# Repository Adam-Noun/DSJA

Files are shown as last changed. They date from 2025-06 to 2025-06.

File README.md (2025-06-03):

Dual Synthetic Jet Actuator 

The proposed capstone project aims to design, fabricate, and experimentally test the performance of a dual 
synthetic jet actuators (SJAs) for flow control in a water tank. SJAs are innovative devices used for fluidic 
active flow control, with applications in aerospace and ground vehicles, electronic device cooling, jet 
vectoring, and mixing in fluid thermal systems. The project will focus on hands-on machining and 
manufacturing to create cost-effective dual SJAs with adjustable exit spacing.

Initial 3D printed Prototype of the device with different orifice geometry to test the effect that it would yield


Testing the deflection of the Piezoelectric Diaphragm with a 3D printed Jig with different weights ontop:



The assembly process of the Final design version of the DSJA: 



Testing Phase of the DSJA where ink would be injected and vortices would be recorded:



Different configuration (vertical or hortizontal) to record if there is any variance that the DSJA would experience depending on the orientation of the device.
[Assembly Experiment.pdf](https://github.com/user-attachments/files/20562680/Assembly.Experiment.pdf)

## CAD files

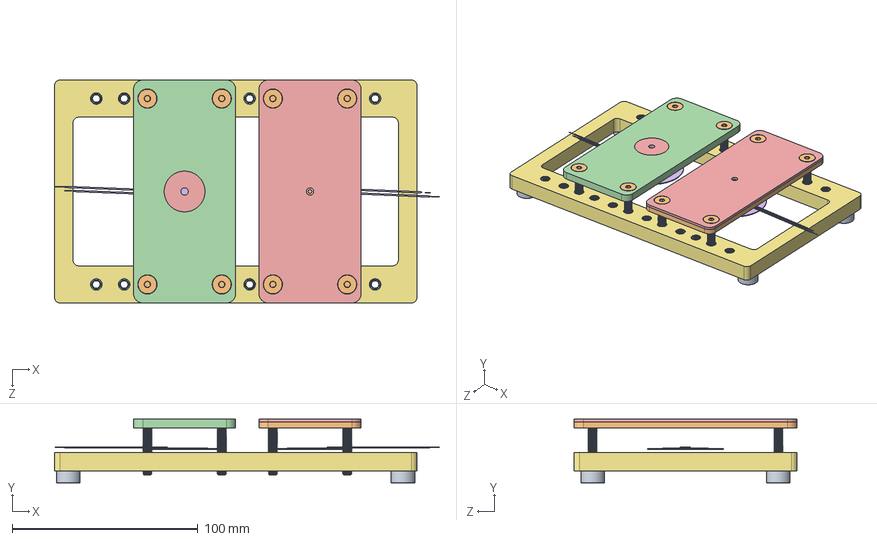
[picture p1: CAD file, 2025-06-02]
PRIMARY ASSEMBLY.SLDASM
207.1 x 34.4 x 120.0 mm
ORIFICE 2 (CIRCULAR) (DEPENDENT) x 2
7BB-41-2L0.stp x 2
FRAME ONE UNIT
Insert M5 D7 L9.5mm x 24
9540K11_Unthreaded Bumper x 4
91263A882_Zinc-Plated Alloy Steel Hex Drive Flat Head Screw x 8

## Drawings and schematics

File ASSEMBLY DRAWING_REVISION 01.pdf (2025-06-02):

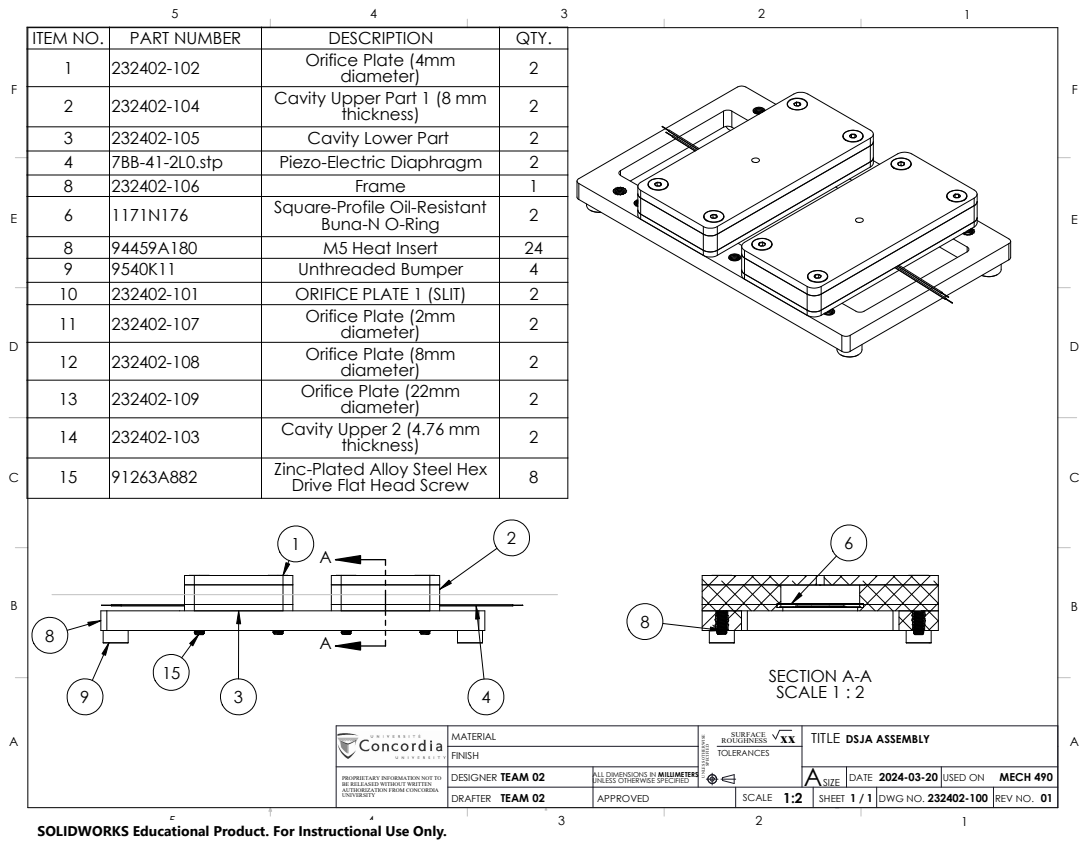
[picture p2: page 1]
TEAM 02; DWG NO.; USED ON; MECH 490; ASIZE; DRAFTER; APPROVED; SCALE 1:2; SHEET; REV NO. 1 / 1; DATE 2024-03-20; DESIGNER; SECTION A-A SCALE 1 : 2

ITEM NO. | PART NUMBER | DESCRIPTION | QTY.
1 | 232402-102 | Orifice Plate (4mm diameter) | 2
2 | 232402-104 | Cavity Upper Part 1 (8 mm thickness) | 2

3 | 232402-105 | Cavity Lower Part | 2
4 | 7BB-41-2L0.stp | Piezo-Electric Diaphragm | 2
8 | 232402-106 | Frame | 1
6 | 1171N176 | Square-Profile Oil-Resistant Buna-N O-Ring | 2

8 | 94459A180 | M5 Heat Insert | 24
9 | 9540K11 | Unthreaded Bumper | 4
10 | 232402-101 | ORIFICE PLATE 1 (SLIT) | 2
11 | 232402-107 | Orifice Plate (2mm diameter) | 2
12 | 232402-108 | Orifice Plate (8mm diameter) | 2
13 14 | 232402-109 232402-103 | Orifice Plate (22mm diameter) Cavity Upper 2 (4.76 mm thickness) | 2 2

15 | 91263A882 | Zinc-Plated Alloy Steel Hex Drive Flat Head Screw | 8

BE RELEASED WITHOUT WRITTEN PROPRIETARY INFORMATION NOT TO | MATERIAL | UNLESS OTHERWISE SPECIFIED | TITLE DSJA ASSEMBLY

UNLESS OTHERWISE SPECIFIED ALL DIMENSIONS IN TEAM 02 MILLIMETERS FINISH | ROUGHNESS SURFACE xx TOLERANCES

AUTHORIZATION FROM CONCORDIA
UNIVERSITY

SOLIDWORKS Educational Product. For Instructional Use Only.

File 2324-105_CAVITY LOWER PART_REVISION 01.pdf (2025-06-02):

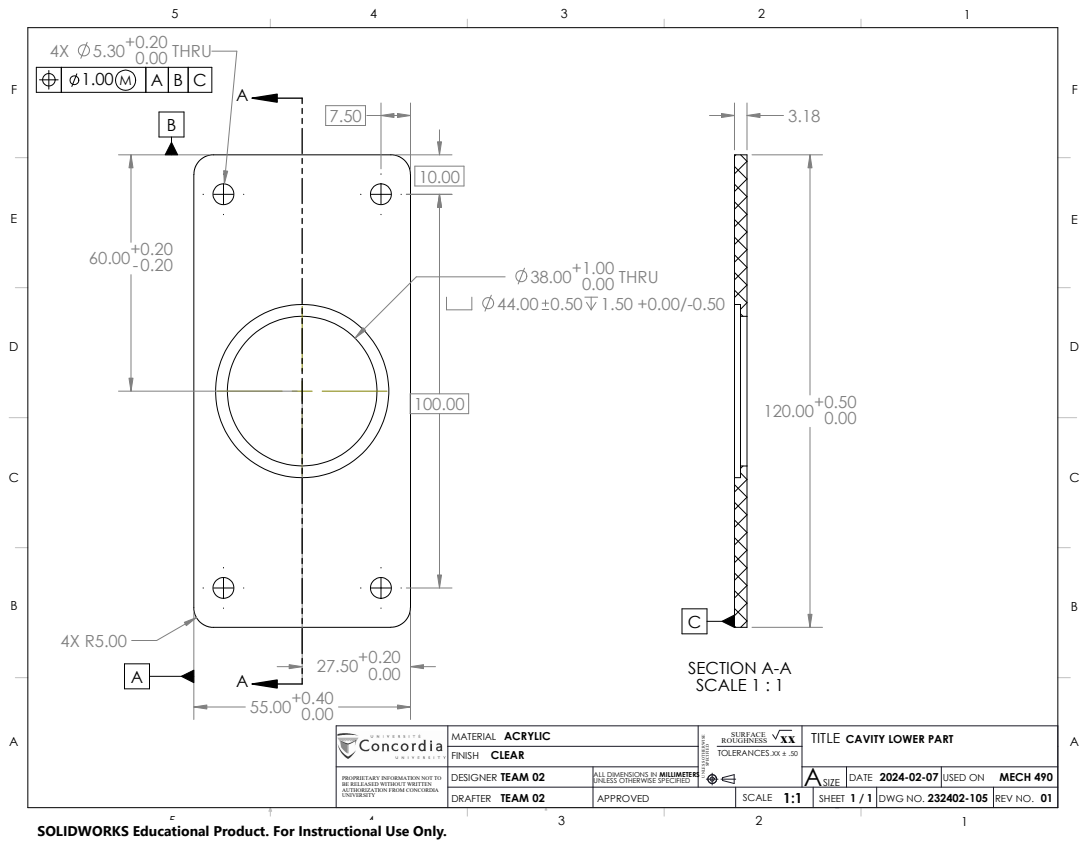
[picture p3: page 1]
TEAM 02; MILLIMETERS SPECIFIED; ACRYLIC; BE RELEASED WITHOUT WRITTEN; UNLESS OTHERWISE SPECIFIED; UNLESS OTHERWISE; ROUGHNESS; DWG NO.; USED ON; MECH 490; FINISH; ASIZE; TOLERANCES.XX ± .50; DRAFTER; APPROVED; SCALE 1:1; SHEET; REV NO. 1 / 1; DATE 2024-02-07; MATERIAL; DESIGNER; PROPRIETARY INFORMATION NOT TO; ALL DIMENSIONS IN; SURFACE; CLEAR; SECTION A-A SCALE 1 : 1; THRU 0.00 4X; 38.00+1.00 0.00 THRU 44.00 0.50

TITLE
CAVITY LOWER PART

AUTHORIZATION FROM CONCORDIA
UNIVERSITY

SOLIDWORKS Educational Product. For Instructional Use Only.

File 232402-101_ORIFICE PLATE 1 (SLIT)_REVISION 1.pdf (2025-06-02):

A

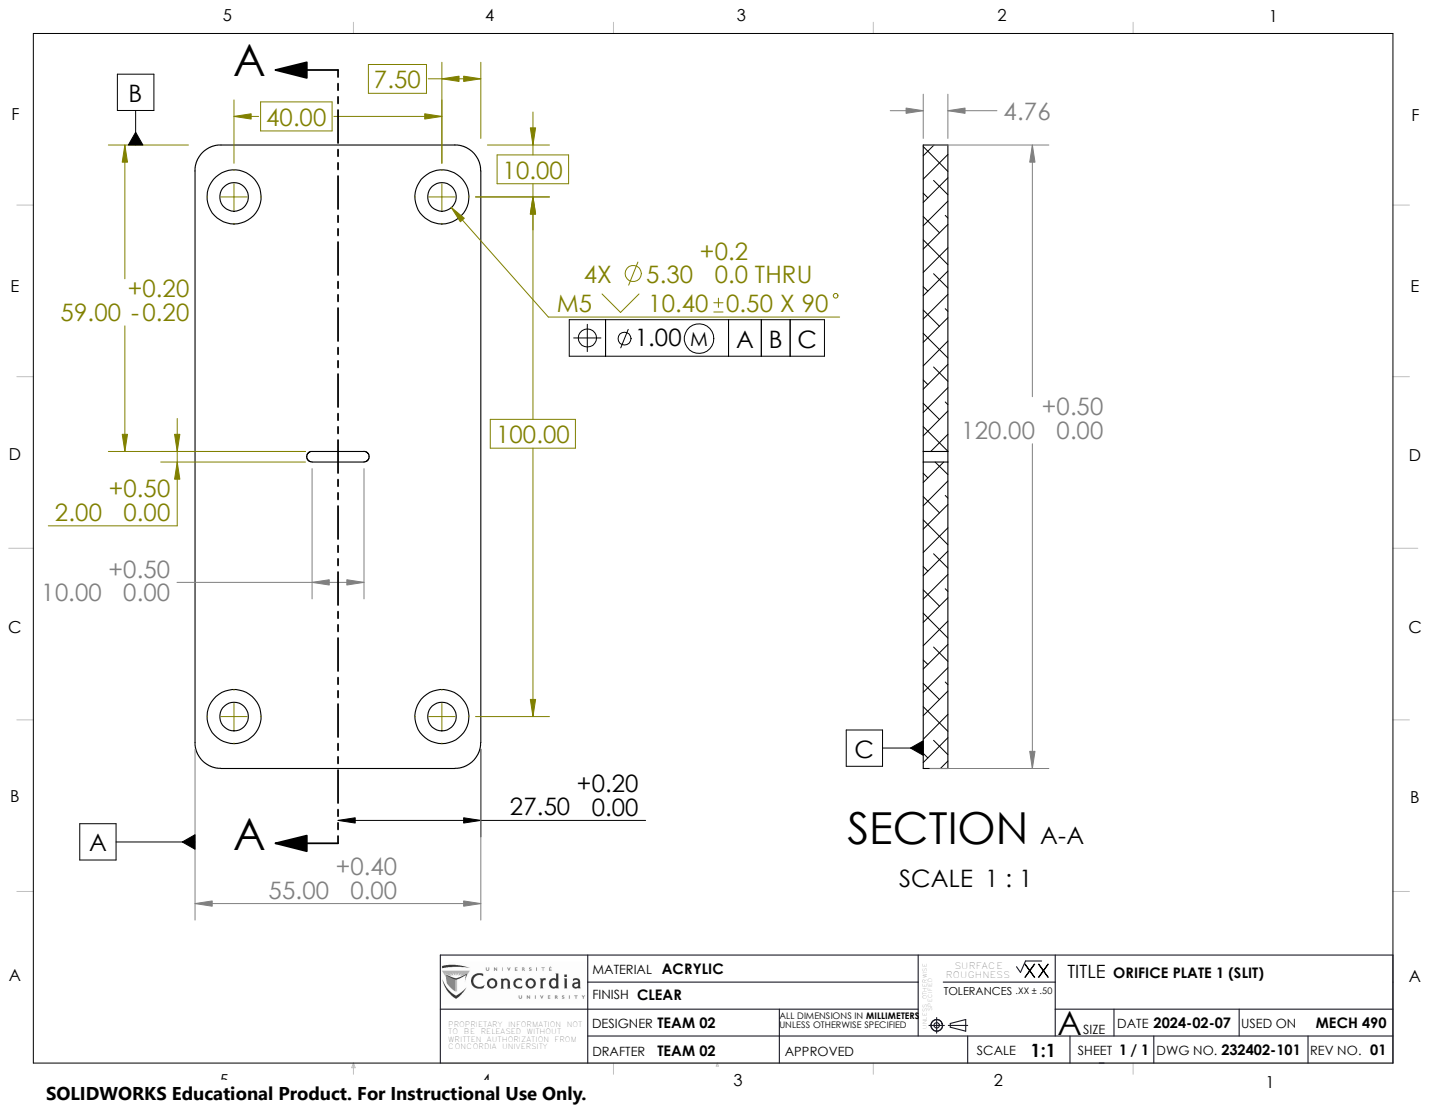
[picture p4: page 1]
TEAM 02; A SPECIFIED; DWG NO.; USED ON; MECH 490; SIZE; MILLIMETERS; DRAFTER; APPROVED; SCALE 1:1; SHEET; REV NO. 1 / 1; DATE 2024-02-07; DESIGNER; +0.2 0.0 THRU; A SECTION A-A; SCALE 1 : 1

MATERIAL ACRYLIC | UNLESS OTHERWISE SURFACE | TITLE ORIFICE PLATE 1 (SLIT)
UNLESS OTHERWISE SPECIFIED CLEAR FINISH | ROUGHNESS XX TOLERANCES .XX ± .50

ALL DIMENSIONS IN

PROPRIETARY INFORMATION NOT
TO BE RELEASED WITHOUT
WRITTEN AUTHORIZATION FROM
CONCORDIA UNIVERSITY

SOLIDWORKS Educational Product. For Instructional Use Only.

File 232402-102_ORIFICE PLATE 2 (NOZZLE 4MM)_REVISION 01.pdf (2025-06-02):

A

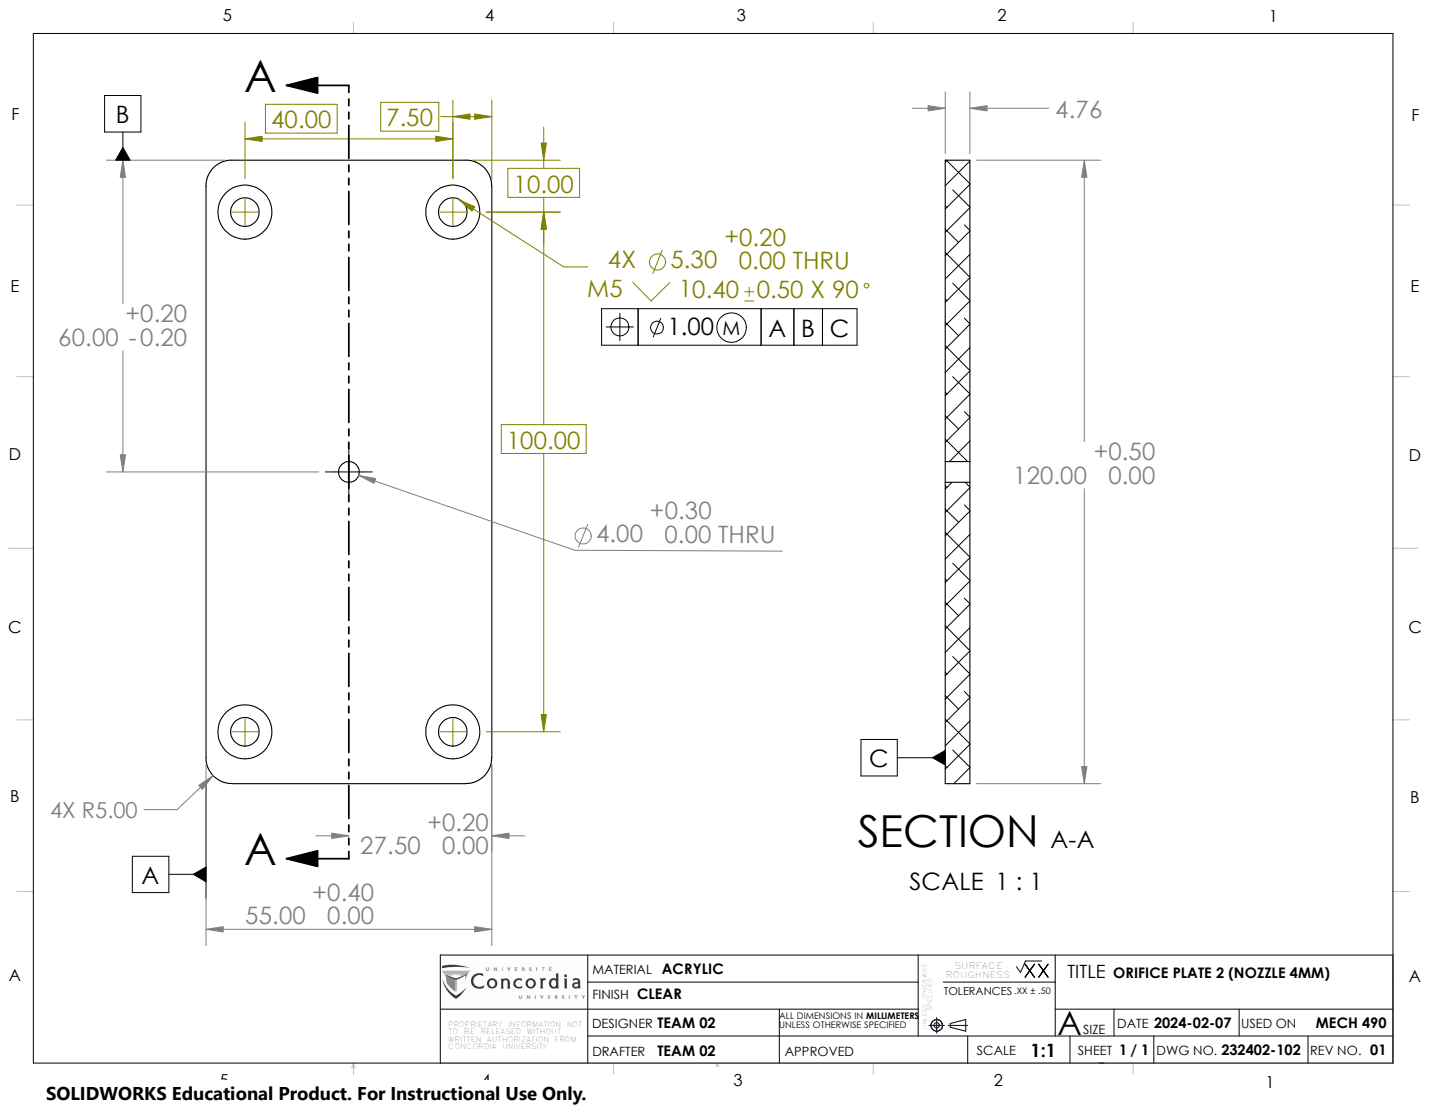
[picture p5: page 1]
TEAM 02; CONCORDIA UNIVERSITY; DWG NO.; USED ON; MECH 490; SIZE; DRAFTER; APPROVED; SCALE 1:1; SHEET; REV NO. 1 / 1; DATE 2024-02-07; DESIGNER; THRU; SECTION A-A; SCALE 1 : 1

MATERIAL ACRYLIC | UNLESS OTHERWISE SURFACE SPECIFIED | TITLE ORIFICE PLATE 2 (NOZZLE 4MM)
UNLESS OTHERWISE SPECIFIED MILLIMETERS CLEAR FINISH | ROUGHNESS XX TOLERANCES .XX ± .50

PROPRIETARY INFORMATION NOT
TO BE RELEASED WITHOUT
WRITTEN AUTHORIZATION FROM

ALL DIMENSIONS IN

SOLIDWORKS Educational Product. For Instructional Use Only.

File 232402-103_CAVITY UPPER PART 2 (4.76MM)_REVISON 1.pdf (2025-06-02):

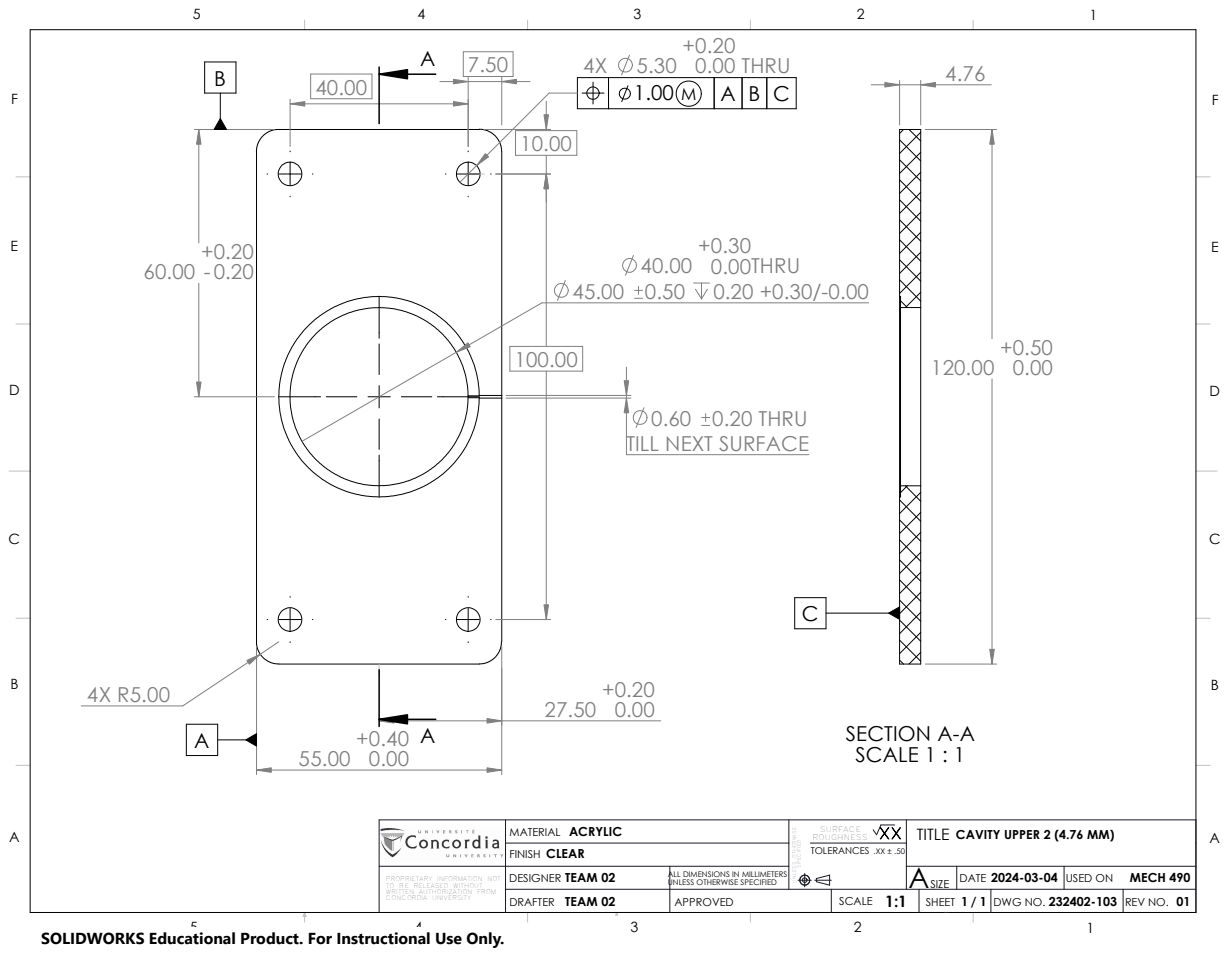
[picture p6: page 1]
TEAM 02; ACRYLIC; CLEAR; SPECIFIED; UNLESS OTHERWISE SPECIFIED; UNLESS OTHERWISE; ROUGHNESS; DWG NO.; USED ON; MECH 490; FINISH; ASIZE; TOLERANCES .XX ± .50; DRAFTER; APPROVED; SCALE 1:1; SHEET; REV NO. 1 / 1; DATE 2024-03-04; MATERIAL; DESIGNER; TO BE RELEASED WITHOUT; SURFACE; 0.20 0.00THRU; THRU; SCALE 1 : 1; SECTION A-A

0.60 0.20 THRU
TILL NEXT SURFACE

TITLE
CAVITY UPPER 2 (4.76 MM)

PROPRIETARY INFORMATION NOT
WRITTEN AUTHORIZATION FROM
CONCORDIA UNIVERSITY

ALL DIMENSIONS IN MILLIMETERS

SOLIDWORKS Educational Product. For Instructional Use Only.

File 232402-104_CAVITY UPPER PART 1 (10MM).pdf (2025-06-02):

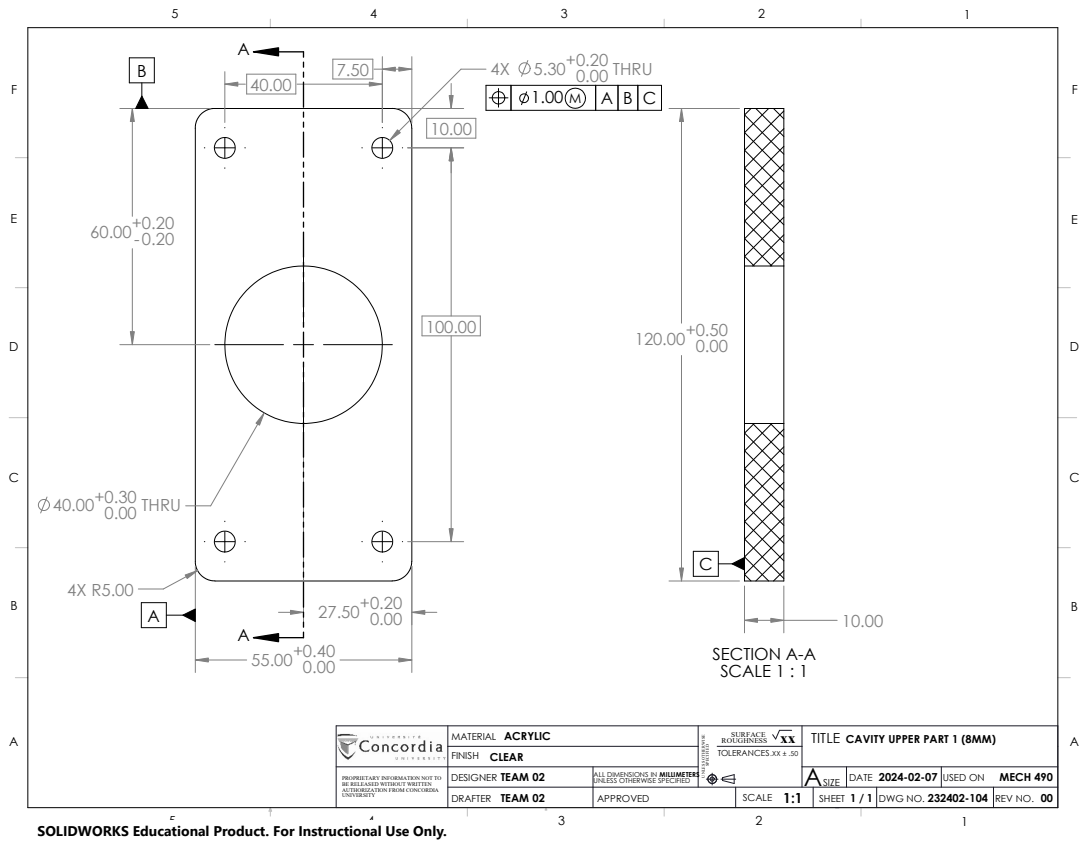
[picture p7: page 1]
TEAM 02; MILLIMETERS; DWG NO.; USED ON; MECH 490; ASIZE; DRAFTER; APPROVED; SCALE 1:1; SHEET; REV NO. 1 / 1; DATE 2024-02-07; DESIGNER; SCALE 1 : 1; SECTION A-A; 5.30+0.20 0.00 THRU; 40.00+0.30 0.00 THRU

PROPRIETARY INFORMATION NOT TO | MATERIAL ACRYLIC | UNLESS OTHERWISE SPECIFIED | TITLE CAVITY UPPER PART 1 (8MM)
UNLESS OTHERWISE SPECIFIED ALL DIMENSIONS IN FINISH CLEAR | ROUGHNESS SURFACE xx TOLERANCES .XX ± .50

BE RELEASED WITHOUT WRITTEN
AUTHORIZATION FROM CONCORDIA
UNIVERSITY

SOLIDWORKS Educational Product. For Instructional Use Only.

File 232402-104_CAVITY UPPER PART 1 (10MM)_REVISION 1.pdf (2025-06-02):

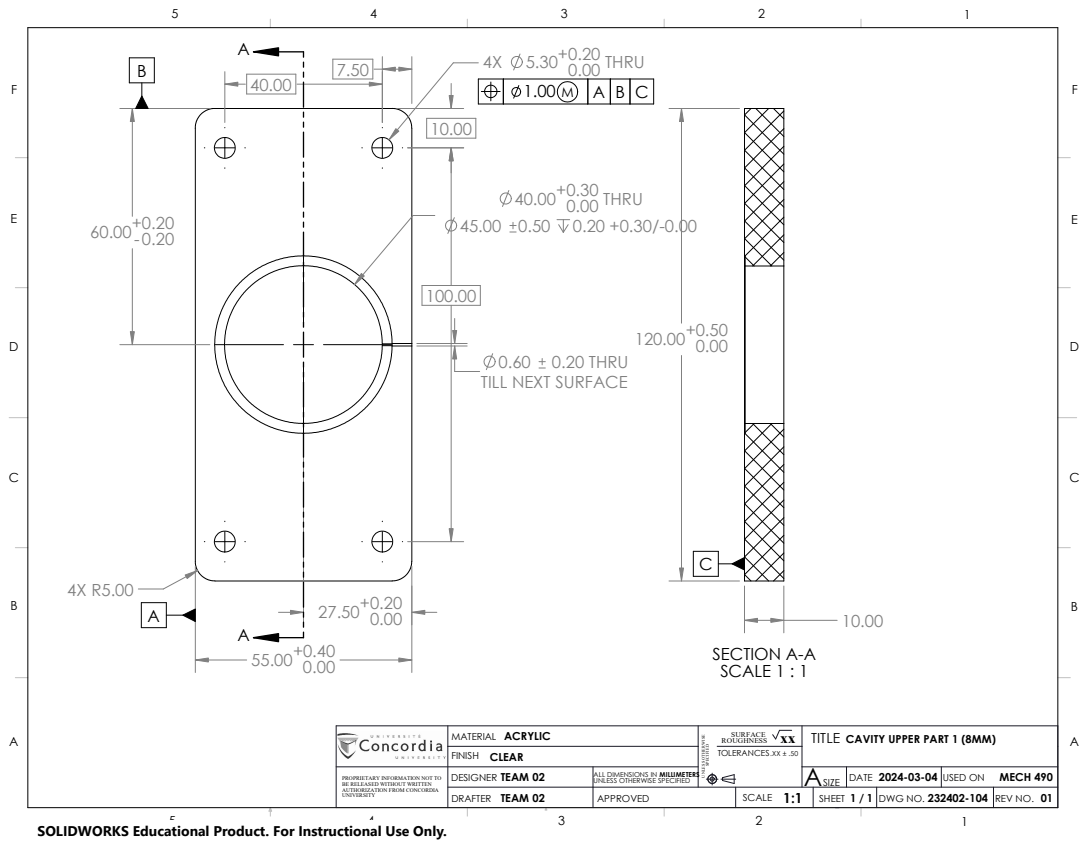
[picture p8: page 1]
SIZE; TEAM 02; MILLIMETERS; DWG NO.; USED ON; MECH 490; DRAFTER; APPROVED; SCALE 1:1; REV NO.; SHEET 1 /; DATE 2024-03-04; DESIGNER; THRU 0.00 45.00 0.20 +0.30/-0.00; 5.30+0.20 0.00 THRU; SCALE 1 : 1; SECTION A-A

0.60 0.20 THRU
TILL NEXT SURFACE

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

BE RELEASED WITHOUT WRITTEN
AUTHORIZATION FROM CONCORDIA
UNIVERSITY

SOLIDWORKS Educational Product. For Instructional Use Only.

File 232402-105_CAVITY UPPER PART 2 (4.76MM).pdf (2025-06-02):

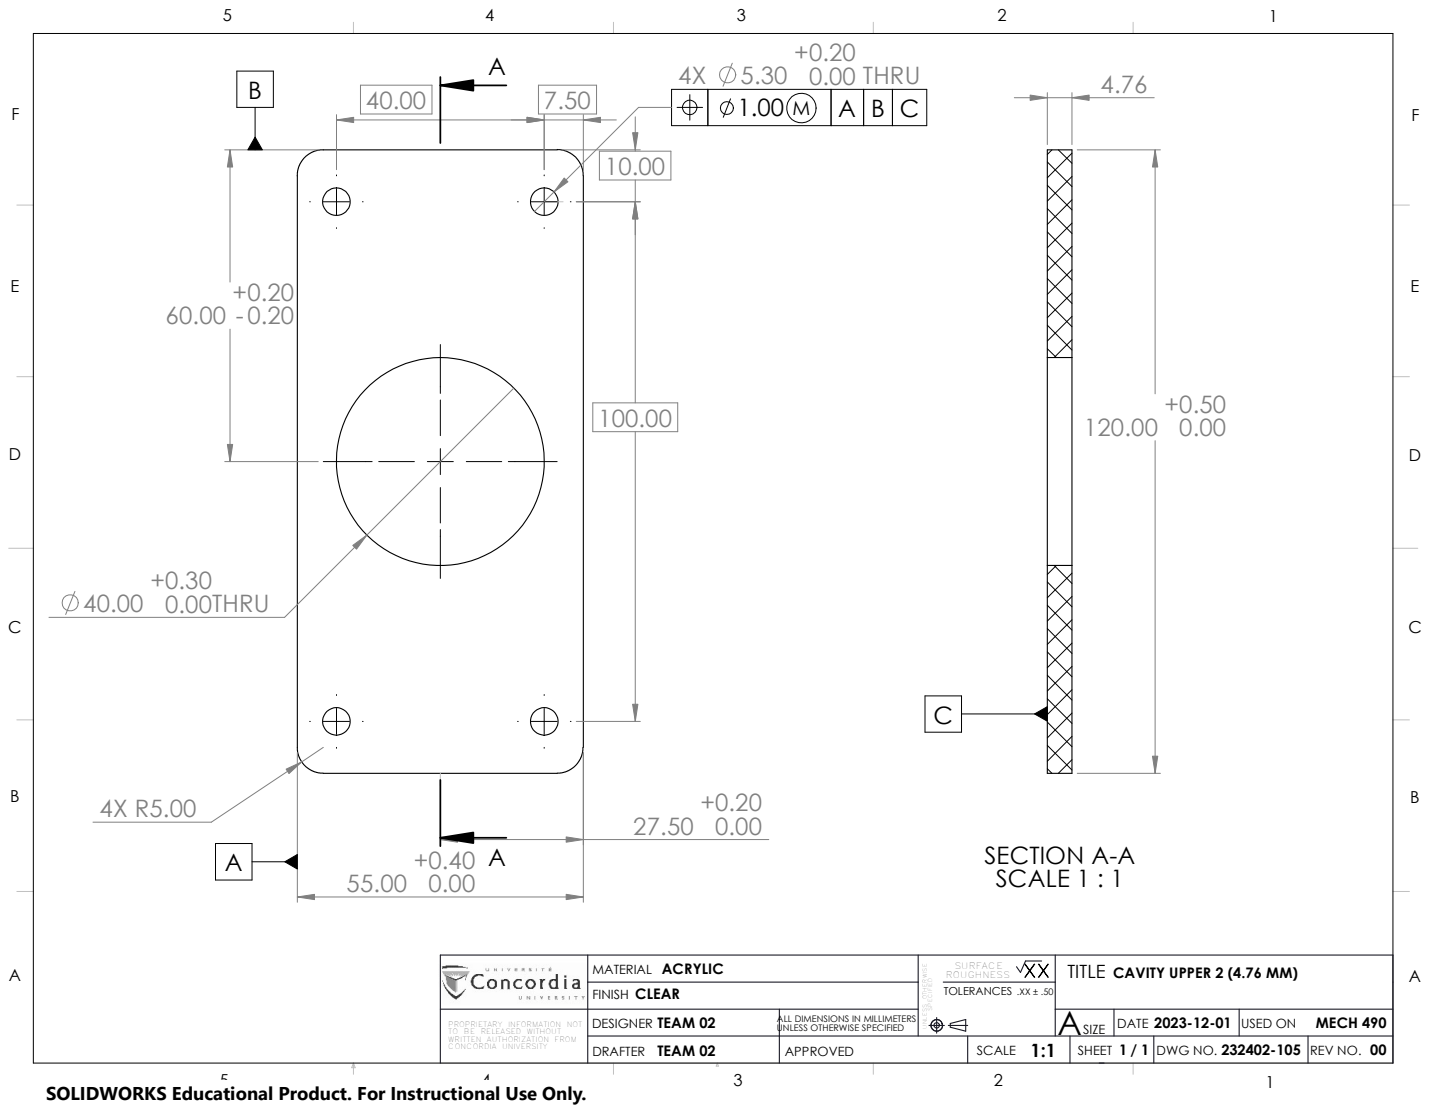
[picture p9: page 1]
TEAM 02; CLEAR; SPECIFIED; ACRYLIC; UNLESS OTHERWISE SPECIFIED; UNLESS OTHERWISE; ROUGHNESS; DWG NO.; USED ON; MECH 490; FINISH; ASIZE; TOLERANCES .XX ± .50; DRAFTER; APPROVED; SCALE 1:1; SHEET; REV NO. 1 / 1; DATE 2023-12-01; MATERIAL; DESIGNER; TO BE RELEASED WITHOUT; SURFACE; SCALE 1 : 1; SECTION A-A; 0.00THRU; +0.20 0.00 THRU

TITLE
CAVITY UPPER 2 (4.76 MM)

PROPRIETARY INFORMATION NOT
WRITTEN AUTHORIZATION FROM
CONCORDIA UNIVERSITY

ALL DIMENSIONS IN MILLIMETERS

SOLIDWORKS Educational Product. For Instructional Use Only.

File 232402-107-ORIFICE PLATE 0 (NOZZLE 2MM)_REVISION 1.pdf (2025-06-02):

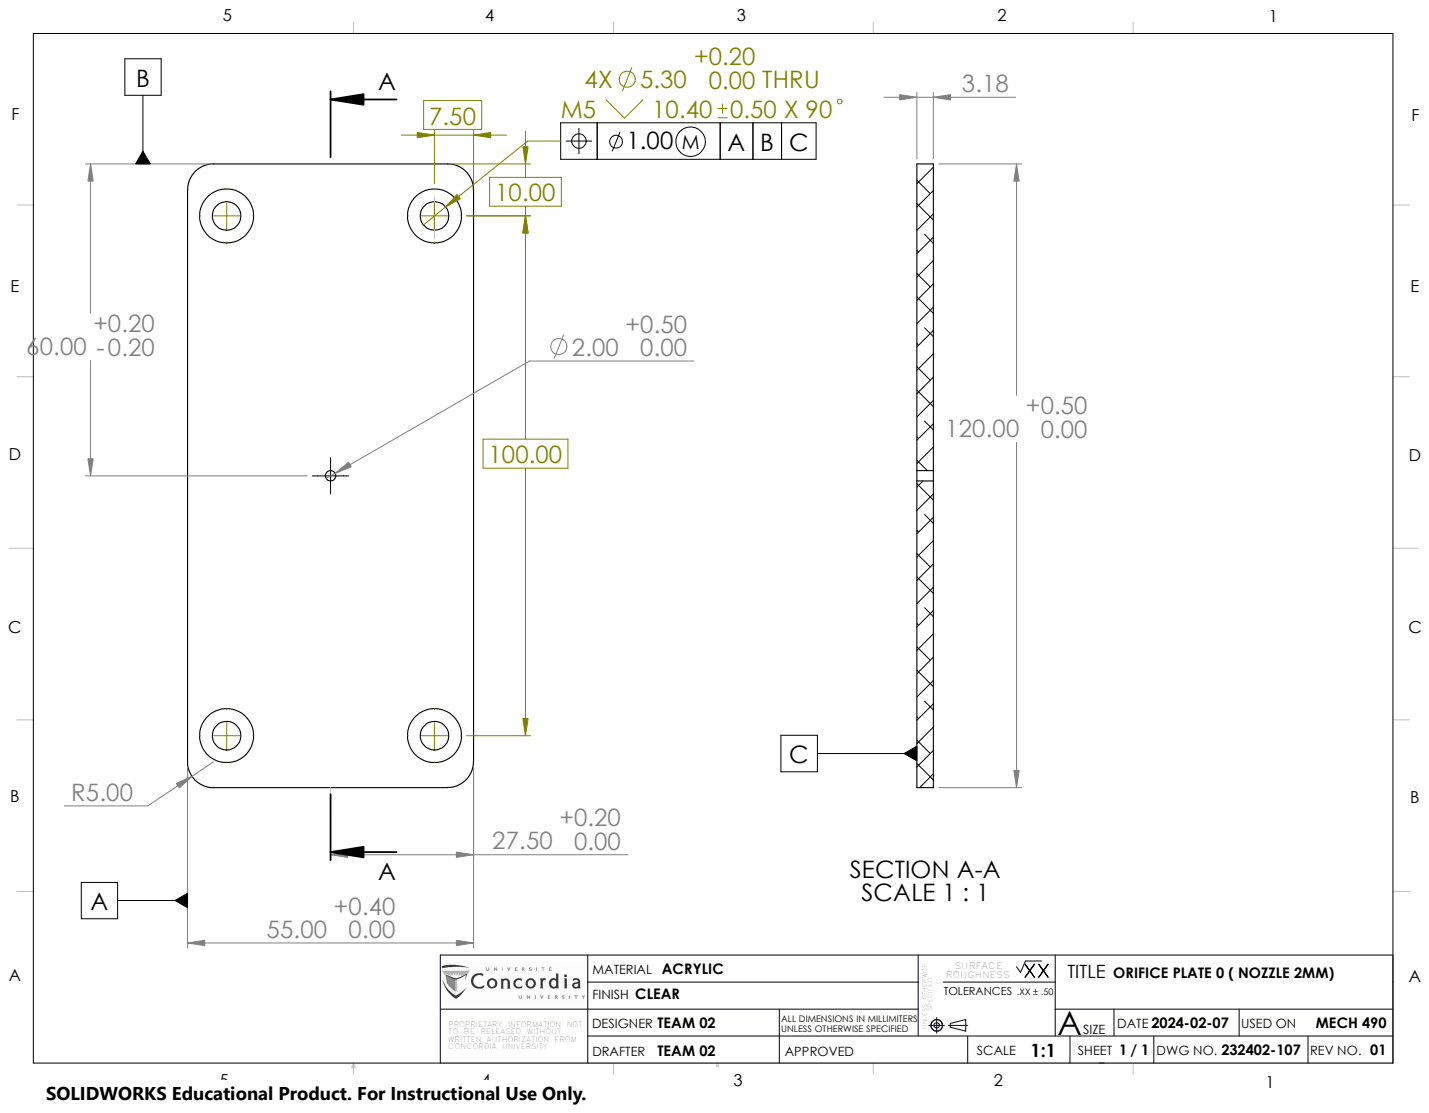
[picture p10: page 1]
TEAM 02; CLEAR; TOLERANCES; ACRYLIC; UNLESS OTHERWISE SPECIFIED; UNLESS OTHERWISE; ROUGHNESS; DWG NO.; USED ON; MECH 490; FINISH; ASIZE SPECIFIED; SURFACE; DRAFTER; APPROVED; SCALE 1:1; SHEET; REV NO. 1 / 1; DATE 2024-02-07; MATERIAL; DESIGNER; +0.20 0.00 THRU; A SECTION A-A SCALE 1 : 1

TITLE
ORIFICE PLATE 0 ( NOZZLE 2MM)

PROPRIETARY INFORMATION NOT
TO BE RELEASED WITHOUT
WRITTEN AUTHORIZATION FROM
CONCORDIA UNIVERSITY

ALL DIMENSIONS IN MILLIMITERS

SOLIDWORKS Educational Product. For Instructional Use Only.

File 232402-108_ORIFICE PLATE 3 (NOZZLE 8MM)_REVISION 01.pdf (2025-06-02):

A

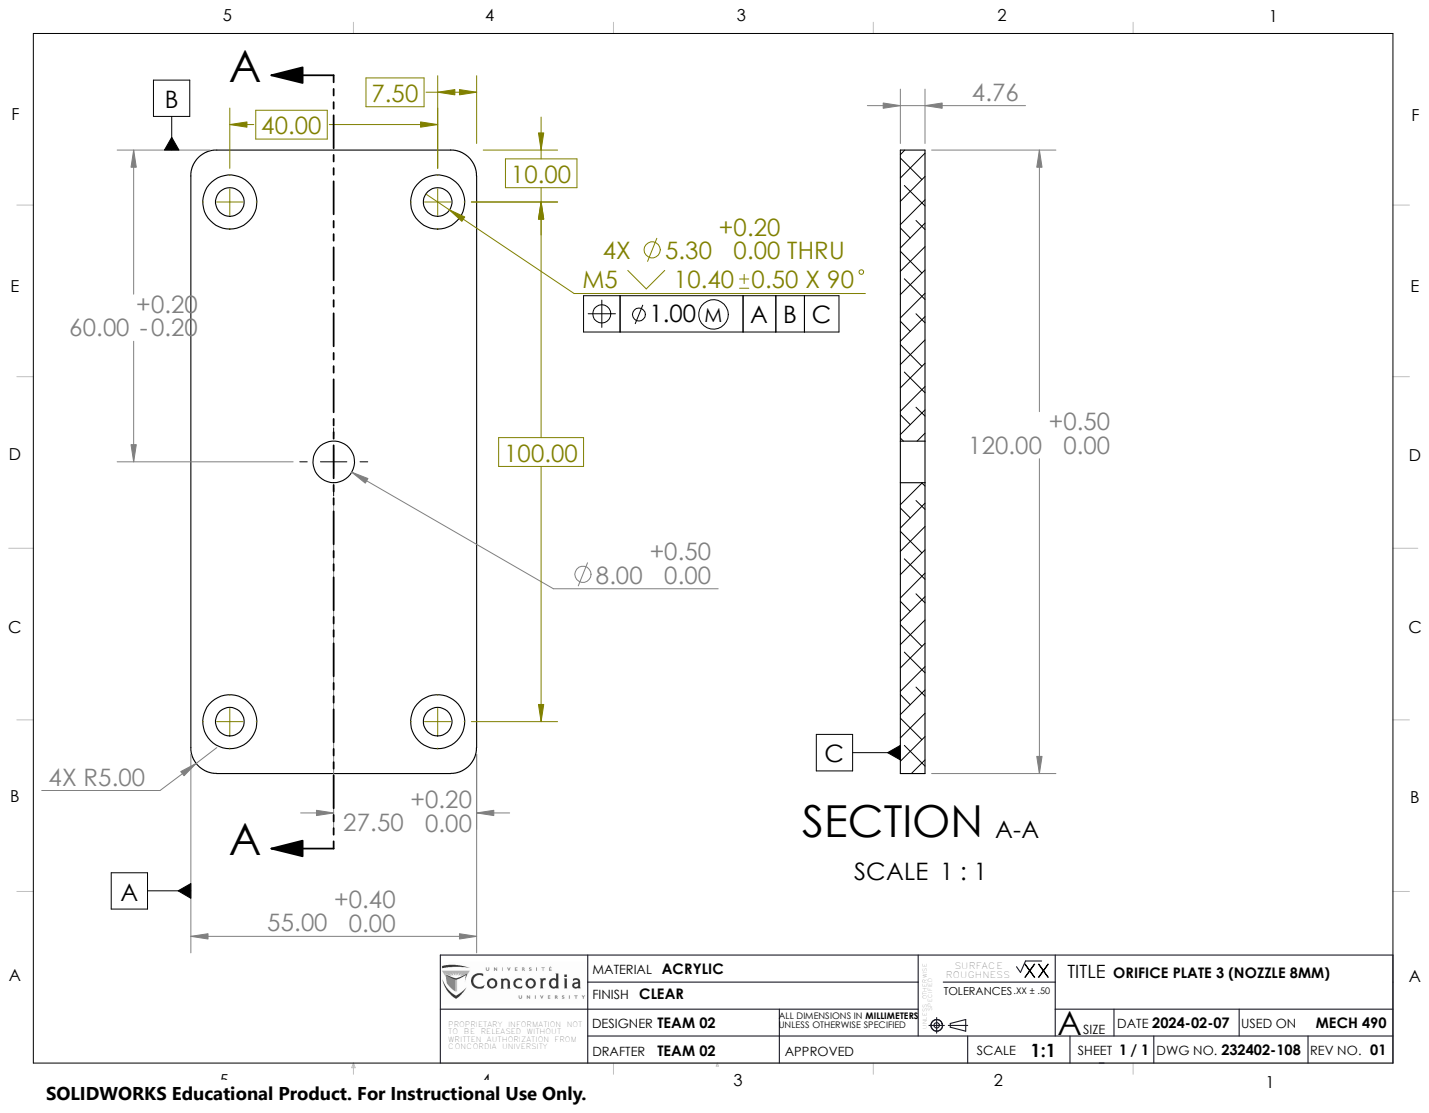
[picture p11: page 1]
TEAM 02; ACRYLIC; MILLIMETERS; SPECIFIED UNLESS OTHERWISE; ROUGHNESS; DWG NO.; USED ON; MECH 490; FINISH; ASIZE; TOLERANCES SURFACE; DRAFTER; APPROVED; SCALE 1:1; SHEET; REV NO. 1 / 1; DATE 2024-02-07; MATERIAL; DESIGNER; .XX ± .50 CLEAR; SECTION A-A; SCALE 1 : 1; +0.20 0.00 THRU

TITLE
ORIFICE PLATE 3 (NOZZLE 8MM)

ALL DIMENSIONS IN
UNLESS OTHERWISE SPECIFIED

PROPRIETARY INFORMATION NOT
TO BE RELEASED WITHOUT
WRITTEN AUTHORIZATION FROM
CONCORDIA UNIVERSITY

SOLIDWORKS Educational Product. For Instructional Use Only.

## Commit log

2025-06-02 Add files via upload
    Assembly of DSJA
    [PRIMARY ASSEMBLY.SLDASM]
2025-06-02 Add files via upload
    Technical Drawings of DSJA assembly
